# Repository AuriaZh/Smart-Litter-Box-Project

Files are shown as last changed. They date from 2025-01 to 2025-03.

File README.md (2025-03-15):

# TECHIN-514 Smart Litter Box Project

# Background
My cat was recently diagnosed with diabetes, so I have to closely monitor her weight and urination frequency. According to my vet, diabetic cats should typically urinate between 2-4 times per day, and anything more than that could indicate poor blood sugar control or other health issues. Other than that, weight management is also essential, so I have to keep daily records of her to prevent unexpected changes in advance. However, cats tend to have an unpredictable litter box routine, which became a big challenge for students like me who must go to school every day. 

# Proposed Solution
This is a smart litter box designed for cats with diabetes. It aims to help owners closely monitor their cats' weight changes and urination frequency. With Bluetooth transmission support, owners can access real-time data anytime through cloud database.
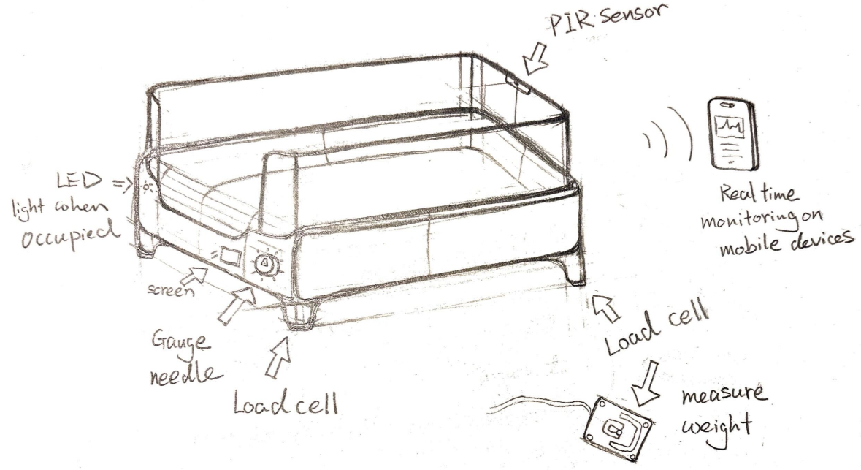
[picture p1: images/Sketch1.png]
General Sketch


# Desired Features
HX711 and 4 Load Cells to measure weight changes and detect urination frequency.
2 Xiao Esp32C3 to transmit data wirelessly via Bluetooth
A stepper motor-driven gauge displays daily urination frequency once it receives data.
Runs on a battery-efficient system optimized for long-term operation.

# System Communication Diagram
This System Communication Diagram shows how the load cells detect weight, the HX711 amplifies the signal, and the Sensor ESP32 processes and sends data via Bluetooth to the Display ESP32, which controls the gauge display and LED indicator for real-time feedback.
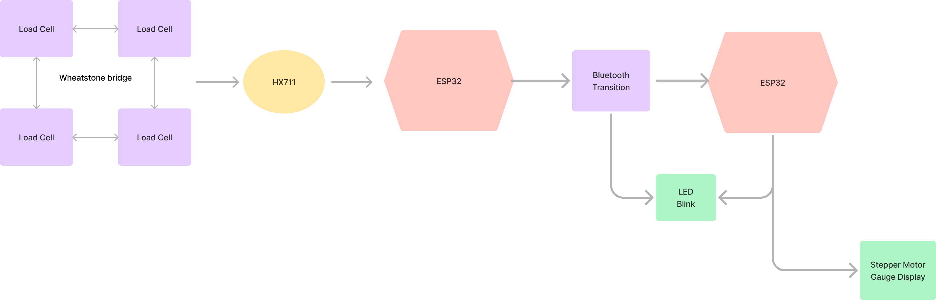
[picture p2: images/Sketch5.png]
General Sketch


# Detailed Diagram
This System Diagram represents the Smart Litter Box for Diabetic Cats. The load cells measure weight, and the HX711 module amplifies and converts the signal. The Sensor ESP32 processes the data and transmits it via Bluetooth to the Display ESP32, which controls the stepper motor gauge display to show visits and the LED as a status indicator.
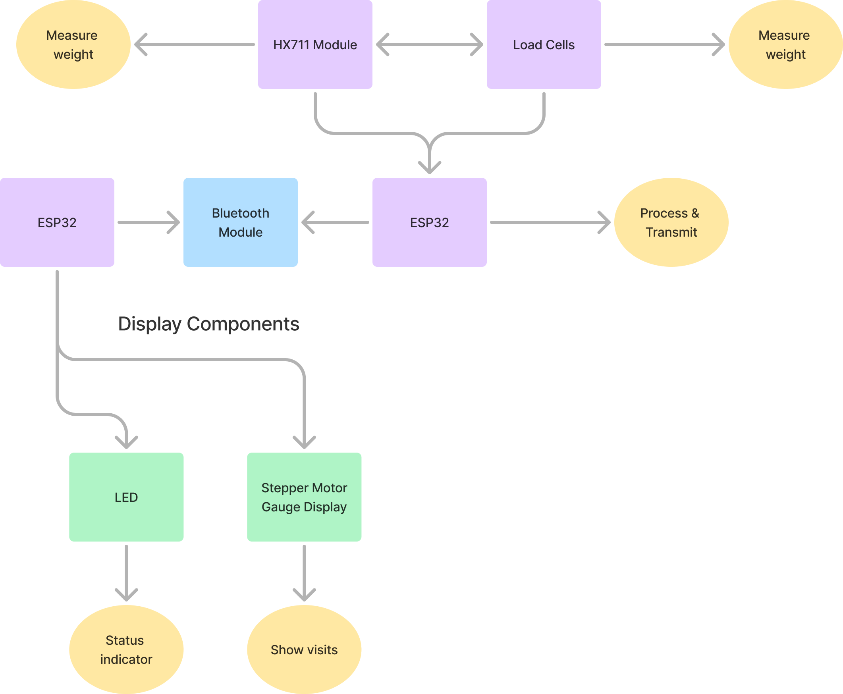
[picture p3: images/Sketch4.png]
General Sketch


# Critical Components & PCB
Schematic diagram
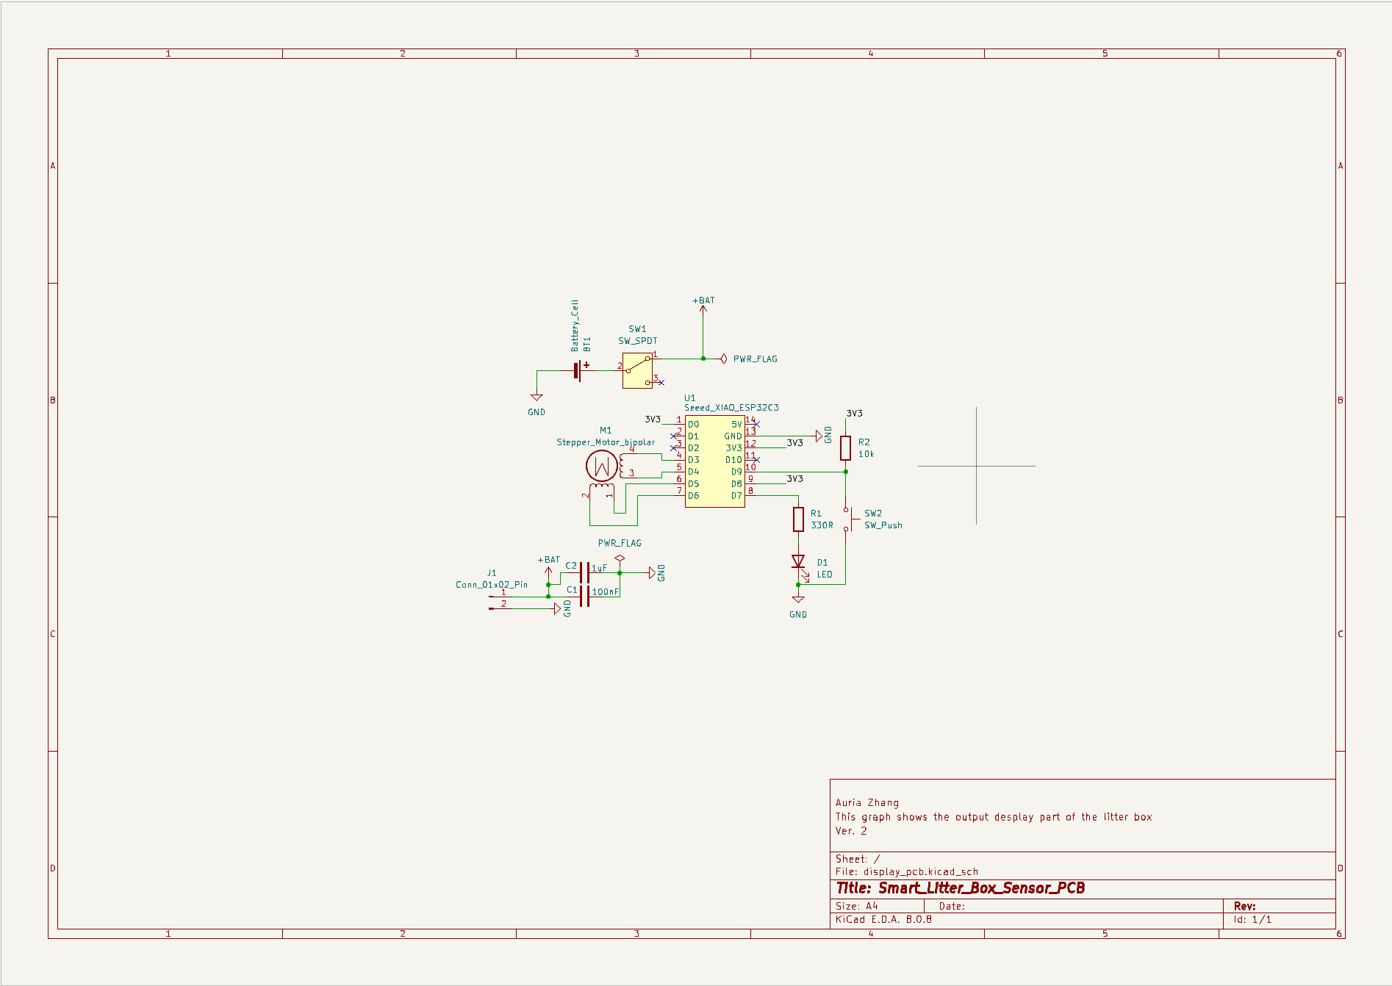
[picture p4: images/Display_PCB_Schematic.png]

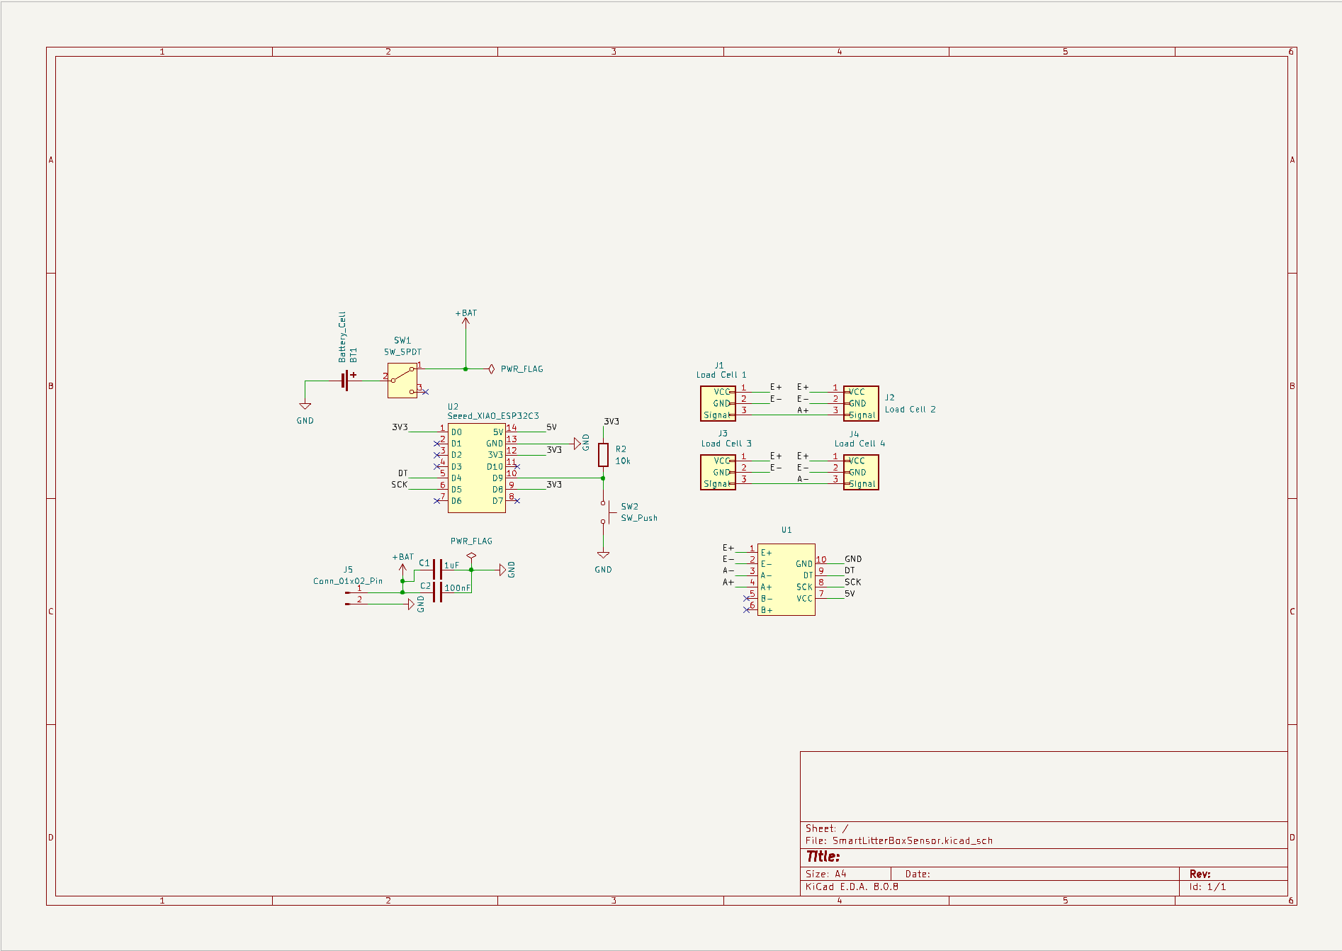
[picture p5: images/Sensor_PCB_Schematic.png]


PCB Design
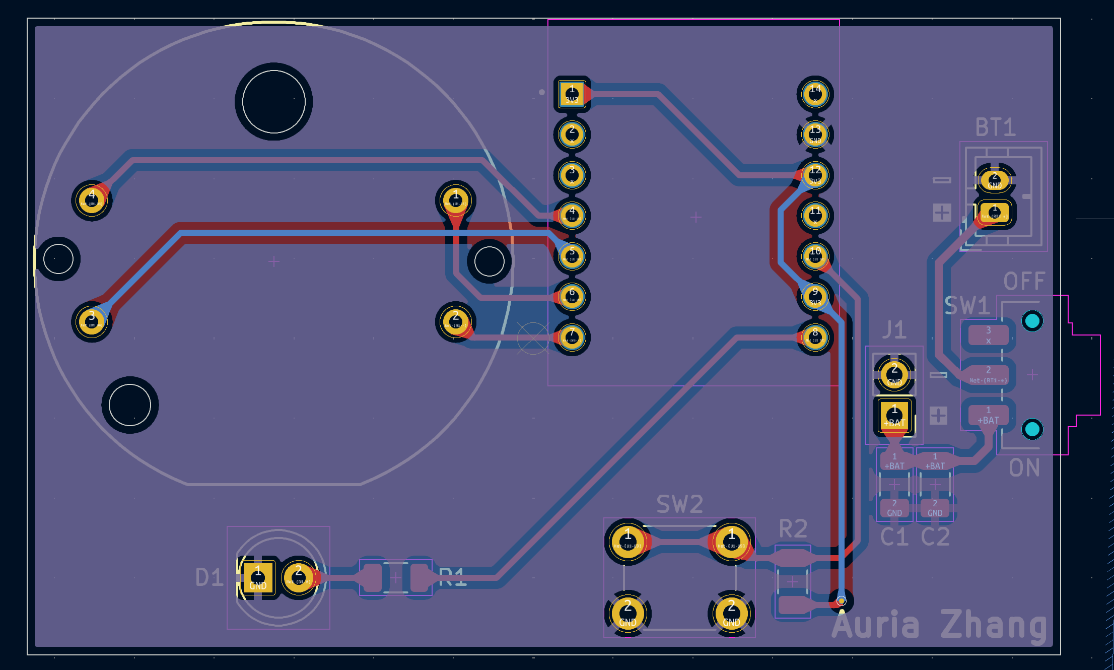
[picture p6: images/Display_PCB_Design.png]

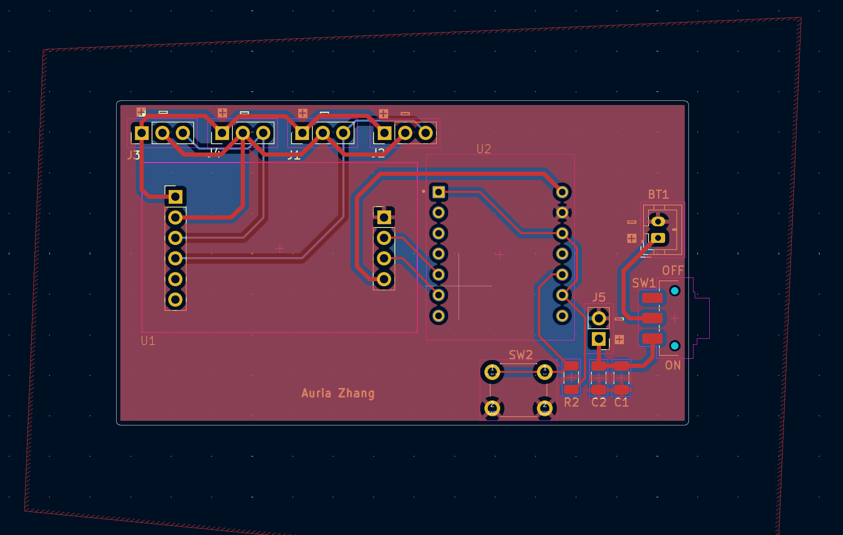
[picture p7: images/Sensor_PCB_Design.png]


Soldered PCB
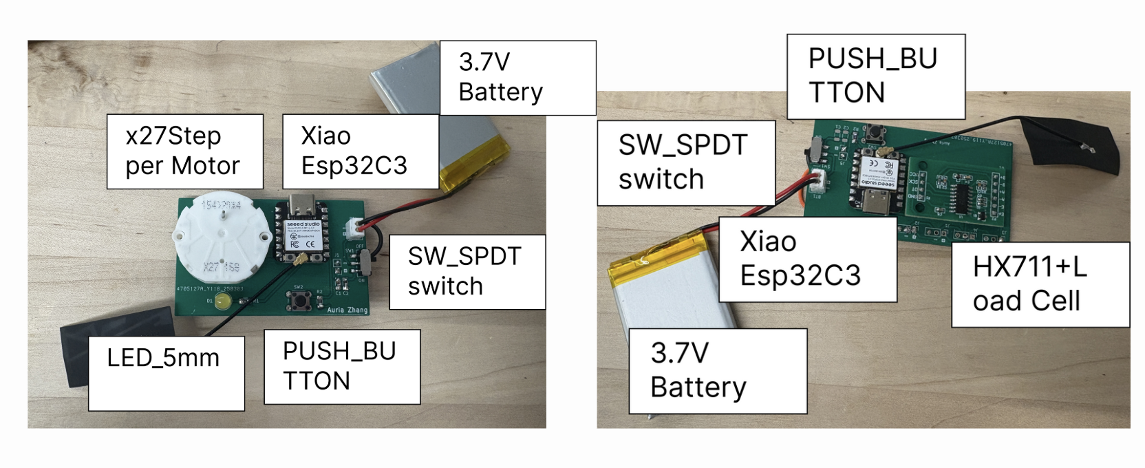
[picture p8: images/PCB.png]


# 3D modeling
Fusion Link: https://a360.co/4hFX8mK

3D model enclosure for sensor device
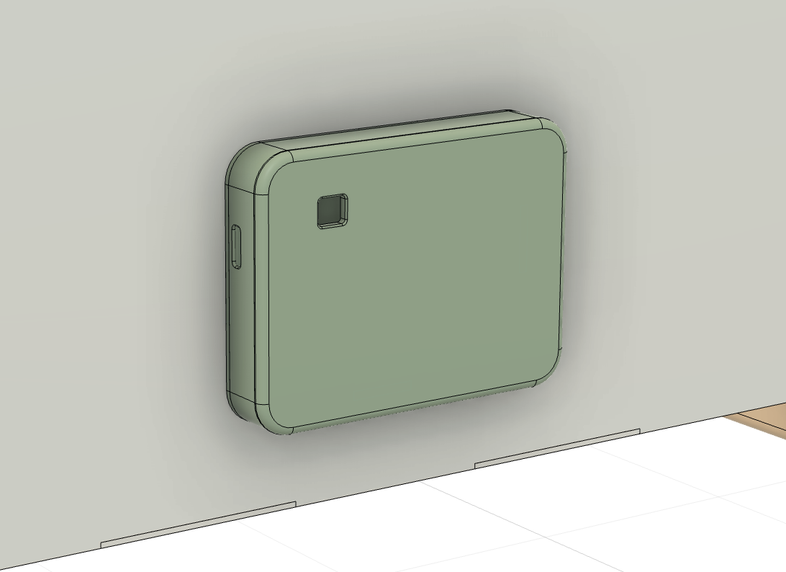
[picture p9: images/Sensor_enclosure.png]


3D model enclosure for display device
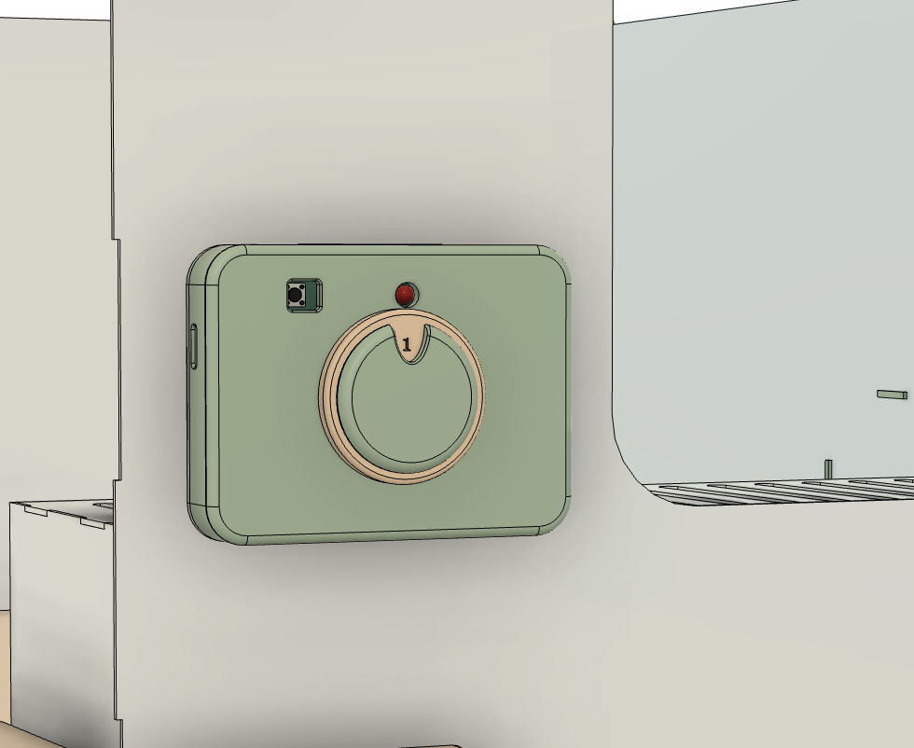
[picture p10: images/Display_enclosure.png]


# Litter box 3D Render
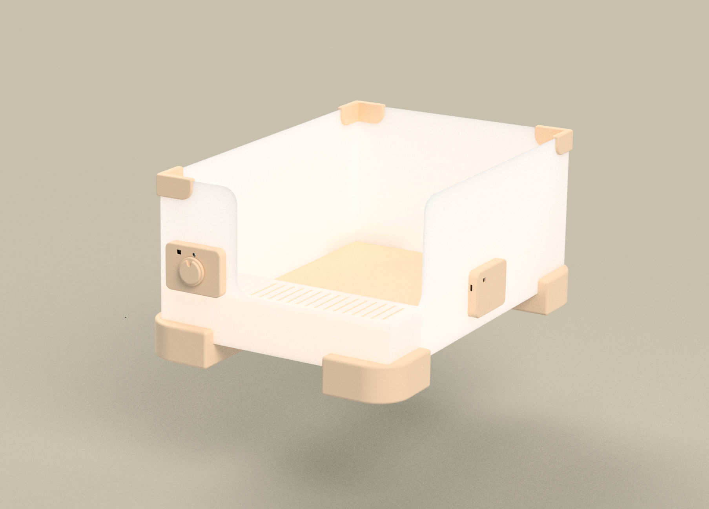
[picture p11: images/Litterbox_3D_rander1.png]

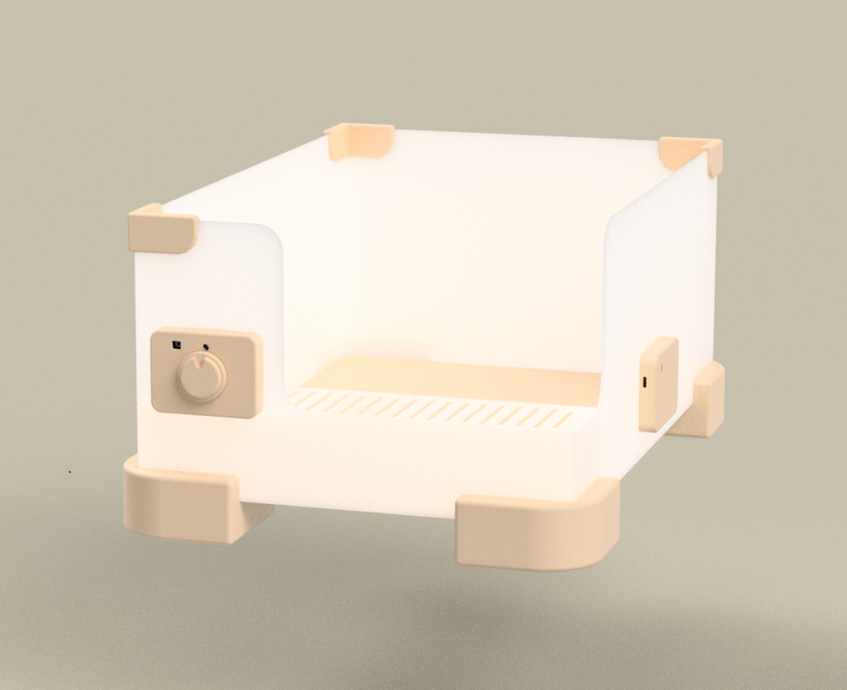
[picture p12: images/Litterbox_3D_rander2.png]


# Prototyping
3D printed devices
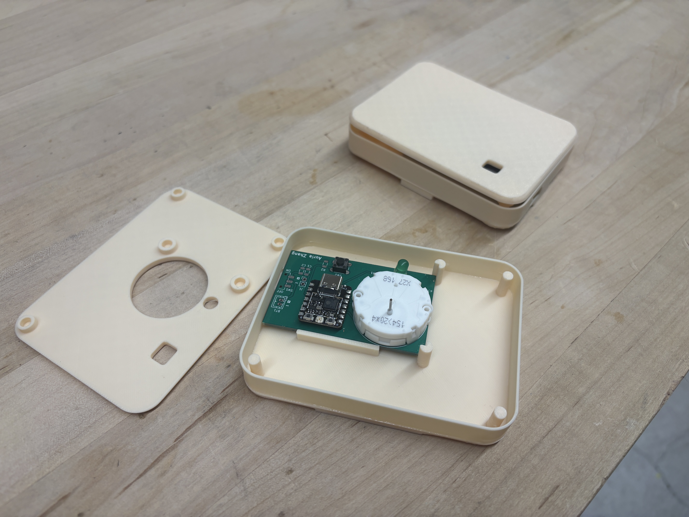
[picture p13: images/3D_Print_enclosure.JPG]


# Final Product
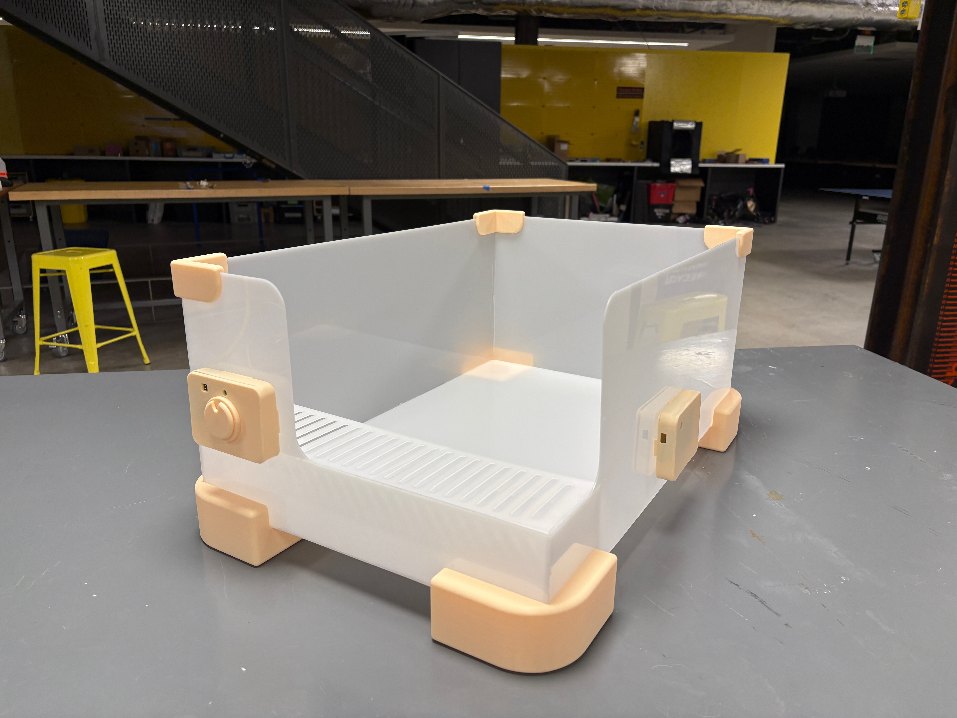
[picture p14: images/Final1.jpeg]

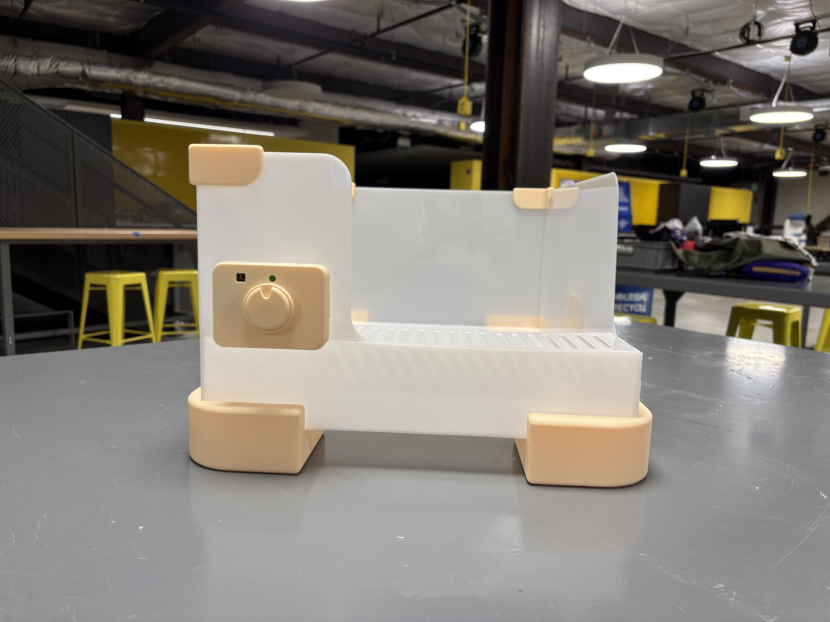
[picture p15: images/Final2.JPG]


# Working Video
Youtube Link: https://youtu.be/_8Va8JSGBe8

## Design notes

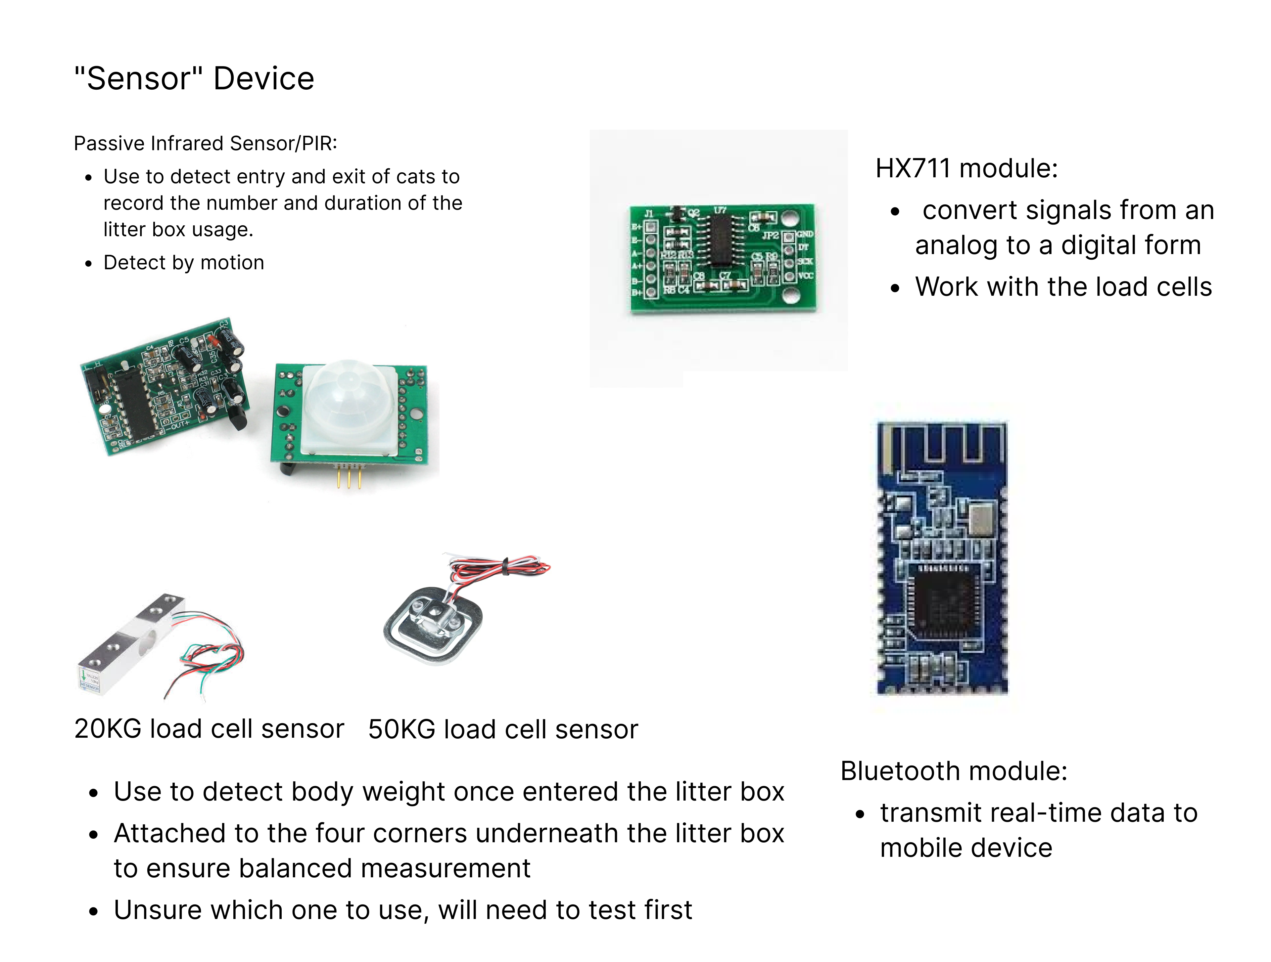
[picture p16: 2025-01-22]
images/Sketch2.png

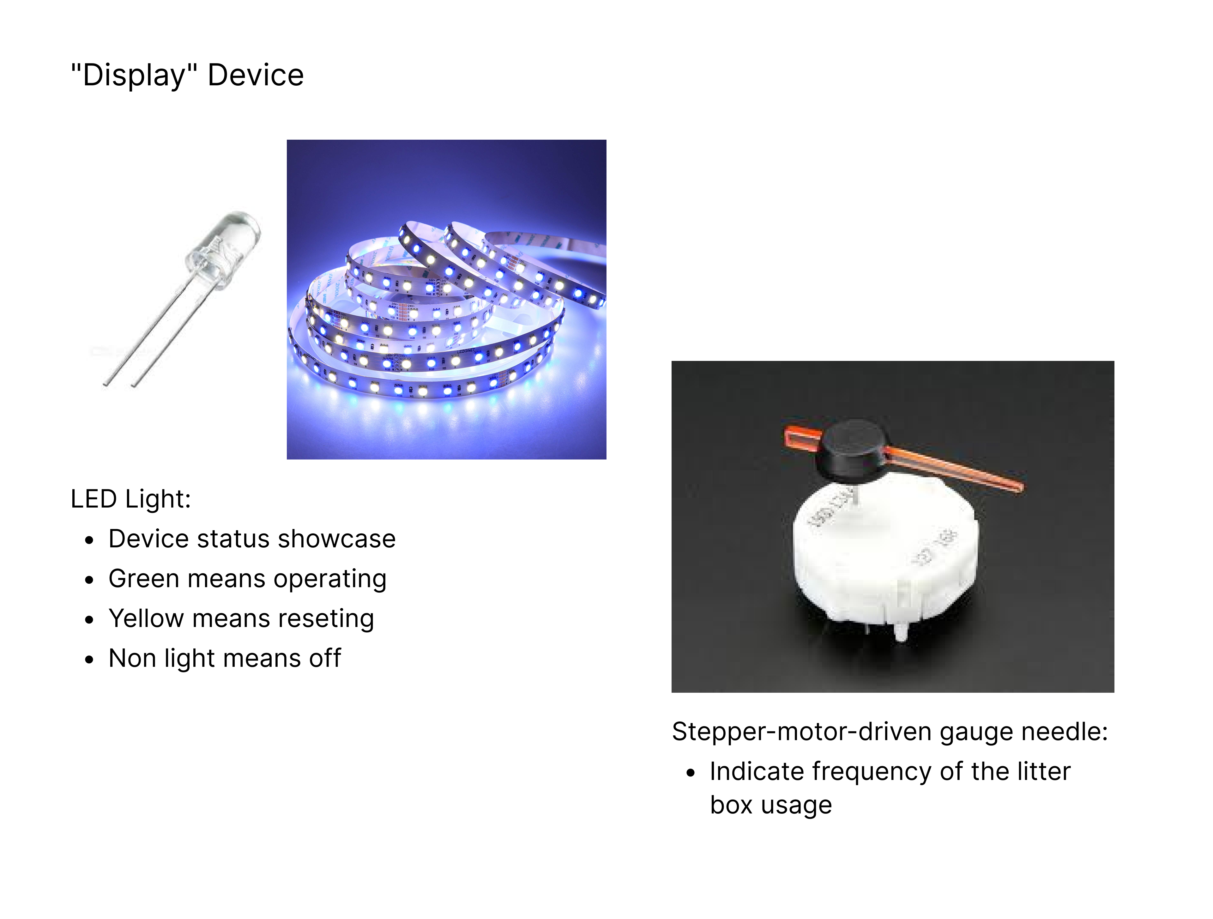
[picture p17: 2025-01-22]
images/Sketch3.png

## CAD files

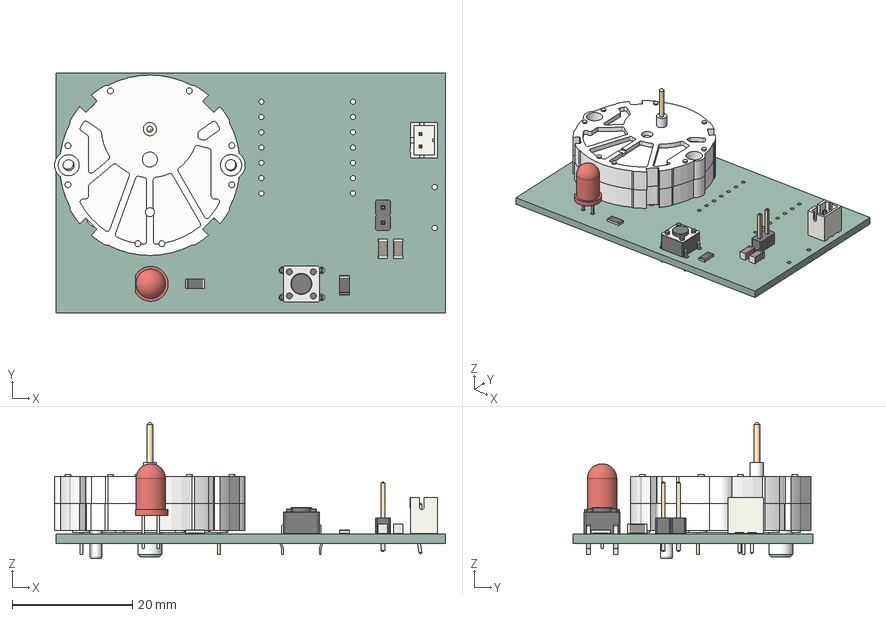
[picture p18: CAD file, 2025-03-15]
PCB_Display/display_pcb.step
65.0 x 39.9 x 22.7 mm
SW_PUSH_6mm
C_1206_3216Metric x 2
LED_D5.0mm
R_1206_3216Metric x 2
PinHeader_1x02_P254mm_Vertical
X27-168-Stepper v5
JST_B2B_PH_K
display_pcb_PCB

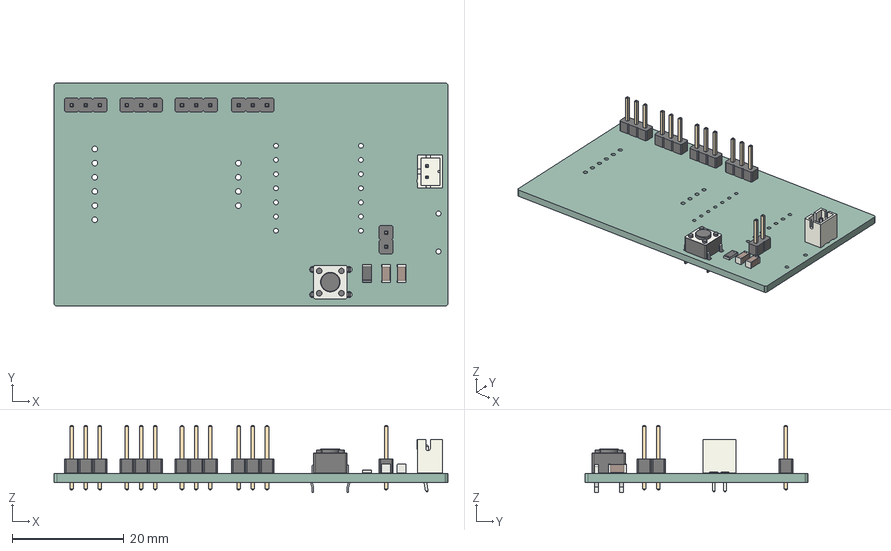
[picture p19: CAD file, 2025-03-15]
PCB_Sensor/PCB_Sensor/SmartLitterBoxSensor.step
70.7 x 40.0 x 12.0 mm
C_1206_3216Metric x 2
PinHeader_1x03_P254mm_Vertical x 4
SW_PUSH_6mm
JST_B2B_PH_K
PinHeader_1x02_P254mm_Vertical
R_1206_3216Metric
SmartLitterBoxSensor_PCB

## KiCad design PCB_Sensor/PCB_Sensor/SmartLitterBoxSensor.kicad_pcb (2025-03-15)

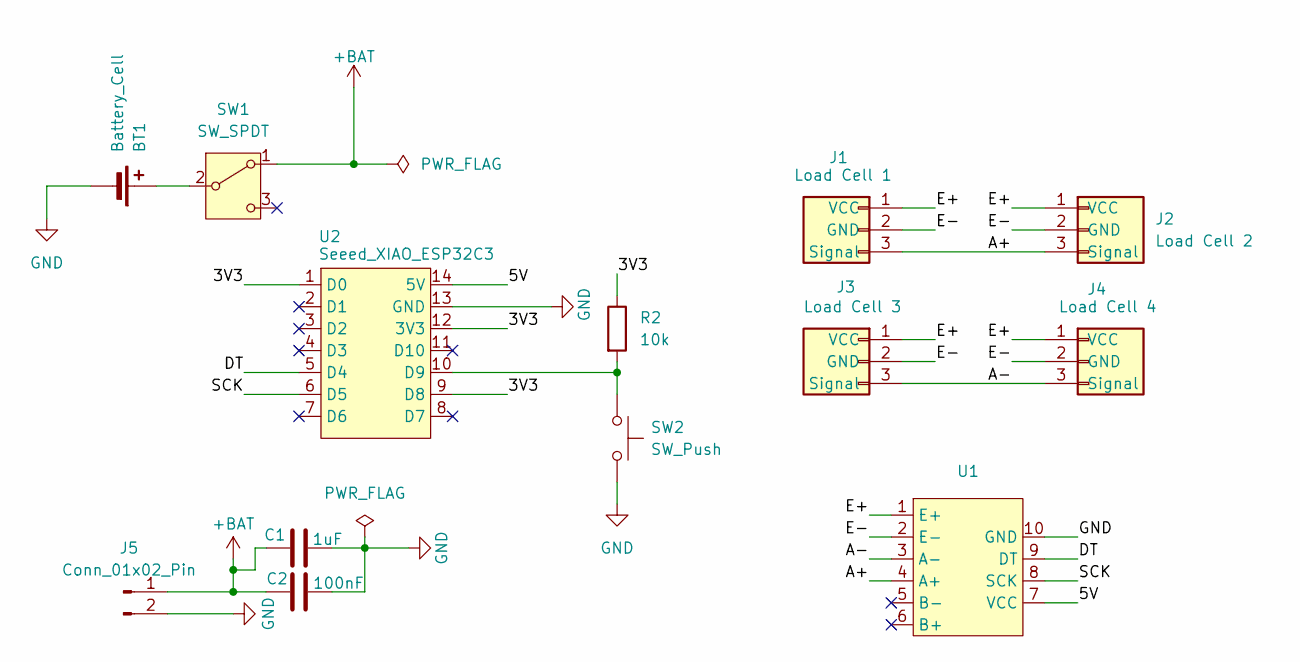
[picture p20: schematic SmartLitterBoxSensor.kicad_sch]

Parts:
BT1: Battery_Cell; JST_PH_B2B-PH-K_1x02_P2.00mm_Vertical
C1: 1uF; C_1206_3216Metric
C2: 100nF; C_1206_3216Metric
J1: Load Cell 1; PinHeader_1x03_P2.54mm_Vertical
J2: Load Cell 2; PinHeader_1x03_P2.54mm_Vertical
J3: Load Cell 3; PinHeader_1x03_P2.54mm_Vertical
J4: Load Cell 4; PinHeader_1x03_P2.54mm_Vertical
J5: Conn_01x02_Pin; PinHeader_1x02_P2.54mm_Vertical
R2: 10k; R_1206_3216Metric
SW1: SW_SPDT; SW_SPDT_CK_JS102011SAQN
SW2: SW_Push; SW_PUSH_6mm
U1: HX711
U2: Seeed_XIAO_ESP32C3; Seeed XIAO ESP32C3

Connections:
+BAT: C1.1, C2.1, J5.1, SW1.1 (A)
/3V3: R2.1, U2.1 (D0), U2.9 (D8), U2.12 (3V3)
/5V: U1.7 (VCC), U2.14 (5V)
/A+: J1.3 (Signal), J2.3 (Signal), U1.4 (A+)
/A-: J3.3 (Signal), J4.3 (Signal), U1.3 (A-)
/DT: U1.9 (DT), U2.5 (D4)
/E+: J1.1 (VCC), J2.1 (VCC), J3.1 (VCC), J4.1 (VCC), U1.1 (E+)
/E-: J1.2 (GND), J2.2 (GND), J3.2 (GND), J4.2 (GND), U1.2 (E-)
/SCK: U1.8 (SCK), U2.6 (D5)
GND: BT1.2 (-), C1.2, C2.2, J5.2, SW2.2, U1.10 (GND), U2.13 (GND)
unnamed: BT1.1 (+), SW1.2 (B)
unnamed: R2.2, SW2.1, U2.10 (D9)

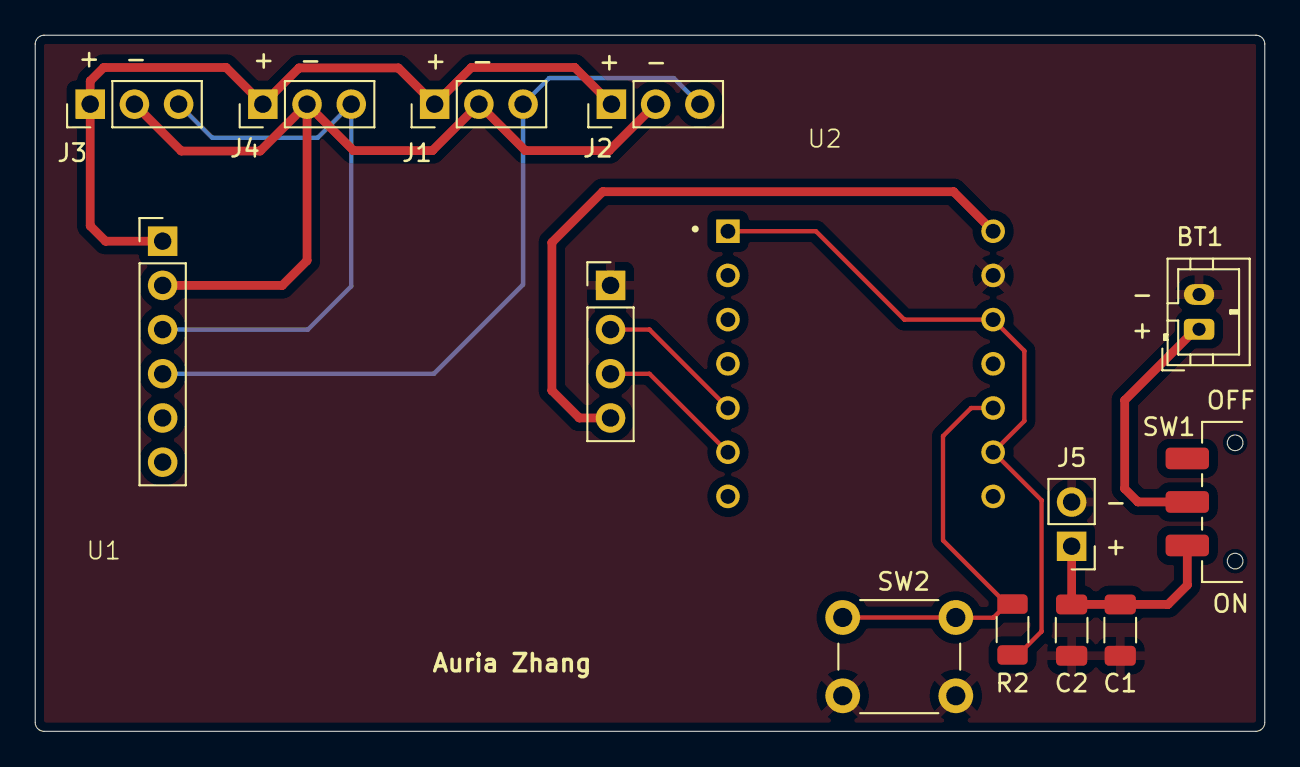
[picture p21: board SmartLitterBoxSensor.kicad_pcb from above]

Board: 2 copper layers, 70.7 x 40.0 mm, 13 parts (0 on the bottom side), 12 nets.

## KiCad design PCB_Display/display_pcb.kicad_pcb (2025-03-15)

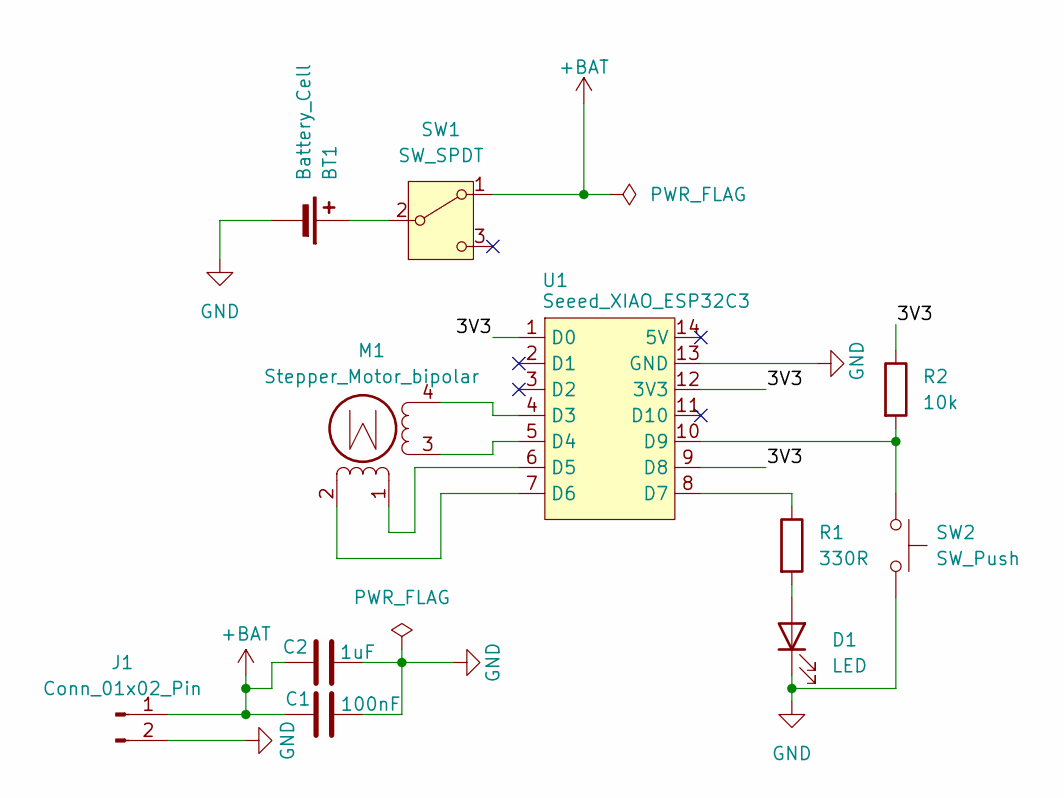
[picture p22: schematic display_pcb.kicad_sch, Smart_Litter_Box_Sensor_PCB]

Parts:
BT1: Battery_Cell; JST_PH_B2B-PH-K_1x02_P2.00mm_Vertical
C1: 100nF; C_1206_3216Metric
C2: 1uF; C_1206_3216Metric
D1: LED; LED_D5.0mm
J1: Conn_01x02_Pin; PinHeader_1x02_P2.54mm_Vertical
M1: Stepper_Motor_bipolar; X27-168
R1: 330R; R_1206_3216Metric
R2: 10k; R_1206_3216Metric
SW1: SW_SPDT; SW_SPDT_CK_JS102011SAQN
SW2: SW_Push; SW_PUSH_6mm
U1: Seeed_XIAO_ESP32C3; Seeed XIAO ESP32C3

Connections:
+BAT: C1.1, C2.1, J1.1, SW1.1 (A)
/3V3: R2.1, U1.1 (D0), U1.9 (D8), U1.12 (3V3)
GND: BT1.2 (-), C1.2, C2.2, D1.1 (K), J1.2, SW2.2, U1.13 (GND)
unnamed: BT1.1 (+), SW1.2 (B)
unnamed: D1.2 (A), R1.2
unnamed: M1.2 (-), U1.7 (D6)
unnamed: M1.4, U1.4 (D3)
unnamed: M1.3, U1.5 (D4)
unnamed: M1.1, U1.6 (D5)
unnamed: R1.1, U1.8 (D7)
unnamed: R2.2, SW2.1, U1.10 (D9)

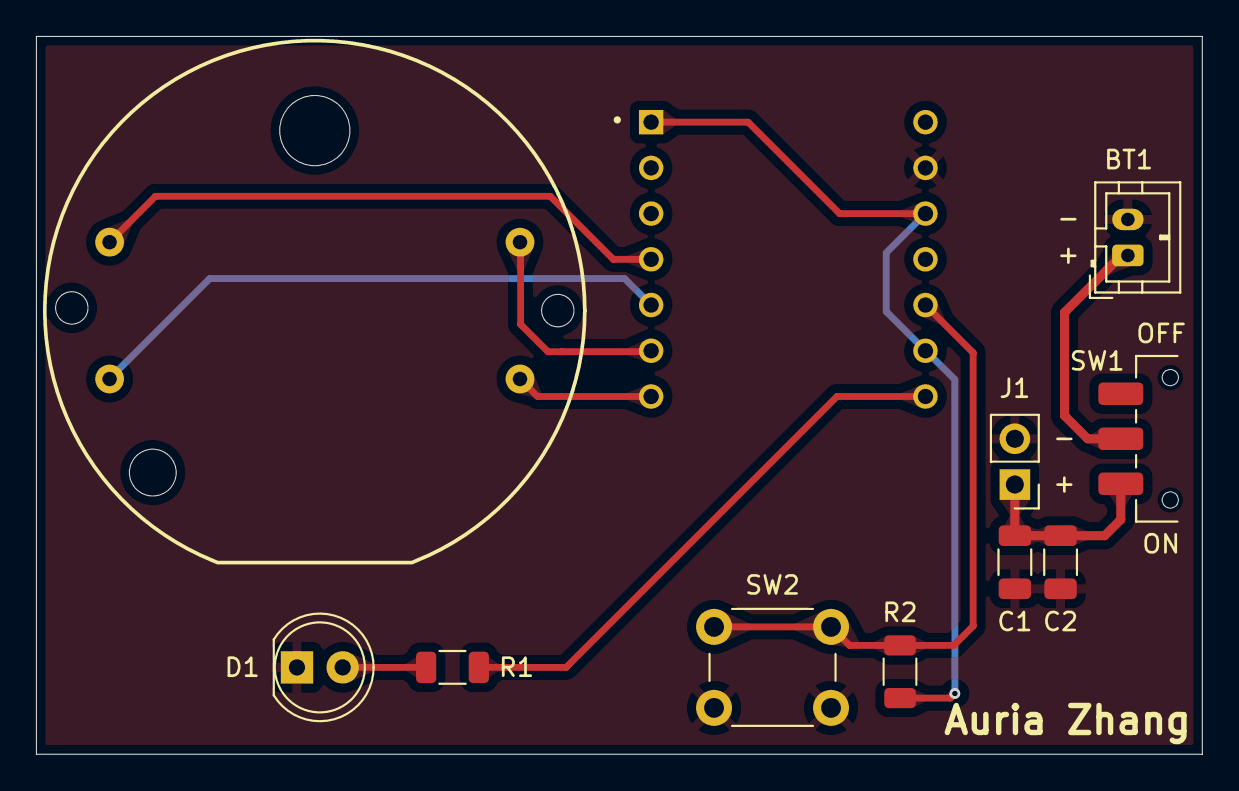
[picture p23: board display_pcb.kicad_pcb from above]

Board: 2 copper layers, 64.8 x 39.9 mm, 11 parts (0 on the bottom side), 11 nets.

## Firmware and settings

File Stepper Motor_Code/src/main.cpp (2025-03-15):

#include <Arduino.h>
#include <BLEDevice.h>
#include <BLEUtils.h>
#include <BLEScan.h>
#include <BLEAdvertisedDevice.h>
#include <AccelStepper.h>

// **Motor 引脚**
#define MOTOR_PIN1 7
#define MOTOR_PIN2 21
#define MOTOR_PIN3 6
#define MOTOR_PIN4 5
#define BUTTON_PIN 9 // 归零按钮 GPIO

AccelStepper stepper(AccelStepper::FULL4WIRE, MOTOR_PIN1, MOTOR_PIN3, MOTOR_PIN2, MOTOR_PIN4);

static BLEUUID serviceUUID("47786ff2-702b-4457-8d4c-bbce01db278c");
static BLEUUID charUUID("2a451022-e0c3-459b-8694-20c0a6aab167");

static boolean doConnect = false;
static boolean connected = false;
static BLERemoteCharacteristic* pRemoteCharacteristic;
static BLEAdvertisedDevice* myDevice;
bool shouldReset = false;  // 是否需要复位指针

void notifyCallback(
  BLERemoteCharacteristic* pBLERemoteCharacteristic,
  uint8_t* pData,
  size_t length,
  bool isNotify) {

    String receivedData = String((char*)pData);
    receivedData.trim();
    float receivedWeight = receivedData.toFloat();

    Serial.print("📡 Received Weight: ");
    Serial.print(receivedWeight, 2);
    Serial.println(" kg");

    if (receivedWeight > 0.1) { // **收到体重数据（猫进入）**
        Serial.println("🐱 Cat Detected! Rotating Stepper Motor...");
        stepper.move(200);
    }
}

class MyClientCallback : public BLEClientCallbacks {
  void onConnect(BLEClient* pclient) {}
  void onDisconnect(BLEClient* pclient) {
    connected = false;
    Serial.println("❌ Disconnected.");
  }
};

bool connectToServer() {
    Serial.println("🔍 Connecting to LoadCell...");
    BLEClient* pClient = BLEDevice::createClient();
    pClient->setClientCallbacks(new MyClientCallback());
    pClient->connect(myDevice);
    Serial.println("✅ Connected!");

    BLERemoteService* pRemoteService = pClient->getService(serviceUUID);
    if (pRemoteService == nullptr) {
      Serial.println("❌ Service Not Found!");
      return false;
    }

    pRemoteCharacteristic = pRemoteService->getCharacteristic(charUUID);
    if (pRemoteCharacteristic == nullptr) {
      Serial.println("❌ Characteristic Not Found!");
      return false;
    }

    pRemoteCharacteristic->registerForNotify(notifyCallback);
    connected = true;
    return true;
}

class MyAdvertisedDeviceCallbacks: public BLEAdvertisedDeviceCallbacks {
  void onResult(BLEAdvertisedDevice advertisedDevice) {
    if (advertisedDevice.haveServiceUUID() && advertisedDevice.isAdvertisingService(serviceUUID)) {
      BLEDevice::getScan()->stop();
      myDevice = new BLEAdvertisedDevice(advertisedDevice);
      doConnect = true;
    }
  }
};

void setup() {
    Serial.begin(115200);
    Serial.println("🚀 Motor BLE Client Starting...");
    BLEDevice::init("Motor");
    pinMode(BUTTON_PIN, INPUT_PULLUP);

    BLEScan* pBLEScan = BLEDevice::getScan();
    pBLEScan->setAdvertisedDeviceCallbacks(new MyAdvertisedDeviceCallbacks());
    pBLEScan->start(5, false);

    stepper.setMaxSpeed(500);
    stepper.setAcceleration(100);

    Serial.println("🔄 Ready to receive weight data!");
}

void loop() {
    if (doConnect) connectToServer();
    stepper.run();

    // **监听按钮（复位 Motor 位置）**
    if (digitalRead(BUTTON_PIN) == LOW) {
        Serial.println("🔄 Resetting Motor...");
        stepper.move(-stepper.currentPosition());  // 回到 0 位置
        shouldReset = true;
        delay(1000);  // 防止抖动
    }

    if (shouldReset && stepper.distanceToGo() == 0) {
        shouldReset = false;
        Serial.println("✅ Motor Reset Complete.");
    }
}

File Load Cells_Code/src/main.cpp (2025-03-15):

#include <Arduino.h>
#include <HX711.h>
#include <BLEDevice.h>
#include <BLEUtils.h>
#include <BLEServer.h>

#define HX711_DT 6  // HX711 DT 连接 ESP32 GPIO6
#define HX711_SCK 7 // HX711 SCK 连接 ESP32 GPIO7
#define BUTTON_PIN 9 // 归零按钮 GPIO

HX711 scale;
float calibration_factor = 1000.0;  // 需要根据你的 Load Cell 校准
float currentWeight = 0.0;

// **BLE UUID**
#define SERVICE_UUID        "47786ff2-702b-4457-8d4c-bbce01db278c"
#define CHARACTERISTIC_UUID "2a451022-e0c3-459b-8694-20c0a6aab167"

BLEServer *pServer = NULL;
BLECharacteristic *pCharacteristic = NULL;

void setup() {
    Serial.begin(115200);
    pinMode(BUTTON_PIN, INPUT_PULLUP);
    
    Serial.println("🐱 Load Cell BLE Server Starting...");
    
    // **初始化 Load Cell**
    scale.begin(HX711_DT, HX711_SCK);
    scale.set_scale(calibration_factor);
    scale.tare();  // 去皮

    // **初始化 BLE**
    BLEDevice::init("LoadCell");
    pServer = BLEDevice::createServer();
    BLEService *pService = pServer->createService(SERVICE_UUID);
    pCharacteristic = pService->createCharacteristic(
                        CHARACTERISTIC_UUID,
                        BLECharacteristic::PROPERTY_READ |
                        BLECharacteristic::PROPERTY_NOTIFY);
    
    pCharacteristic->setValue("0");
    pService->start();

    BLEAdvertising *pAdvertising = BLEDevice::getAdvertising();
    pAdvertising->addServiceUUID(SERVICE_UUID);
    BLEDevice::startAdvertising();

    Serial.println("🚀 BLE Service Started!");
}

void loop() {
    if (scale.is_ready()) {
        currentWeight = scale.get_units(5); // 取 5 次平均值
        Serial.print("⚖️  Stable Weight: ");
        Serial.print(currentWeight, 2);
        Serial.println(" kg");

        // 发送数据
        String weightStr = String(currentWeight, 2);
        pCharacteristic->setValue(weightStr.c_str());
        pCharacteristic->notify();
    } else {
        Serial.println("❌ HX711 NOT RESPONDING!");
    }

    // **监听按钮（归零 tare）**
    if (digitalRead(BUTTON_PIN) == LOW) {
        Serial.println("🔄 Resetting Scale...");
        scale.tare();
        delay(1000);  // 防止抖动
    }

    delay(500);
}

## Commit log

2025-02-14 Add files via upload
    Update the display part of the PCB
    [display_pcb-B_Cu.gbr, display_pcb-B_Mask.gbr, display_pcb-B_Paste.gbr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]
2025-02-14 Add files via upload
    Upload power analyzing for both sensor and display
    [Sensitivity Analysis-Table 1.csv, System Parameters-Table 1.csv]
2025-03-15 Add files via upload
    Upload code for both Load cells and Stepper Motor devices
2025-03-15 Add files via upload
    Upload updated 2 PCBs
    [SmartLitterBoxSensor-B_Cu.gbr, SmartLitterBoxSensor-B_Mask.gbr, SmartLitterBoxSensor-B_Paste.gbr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]
2025-03-15 Add files via upload
    3D models for litter box and enclosure
